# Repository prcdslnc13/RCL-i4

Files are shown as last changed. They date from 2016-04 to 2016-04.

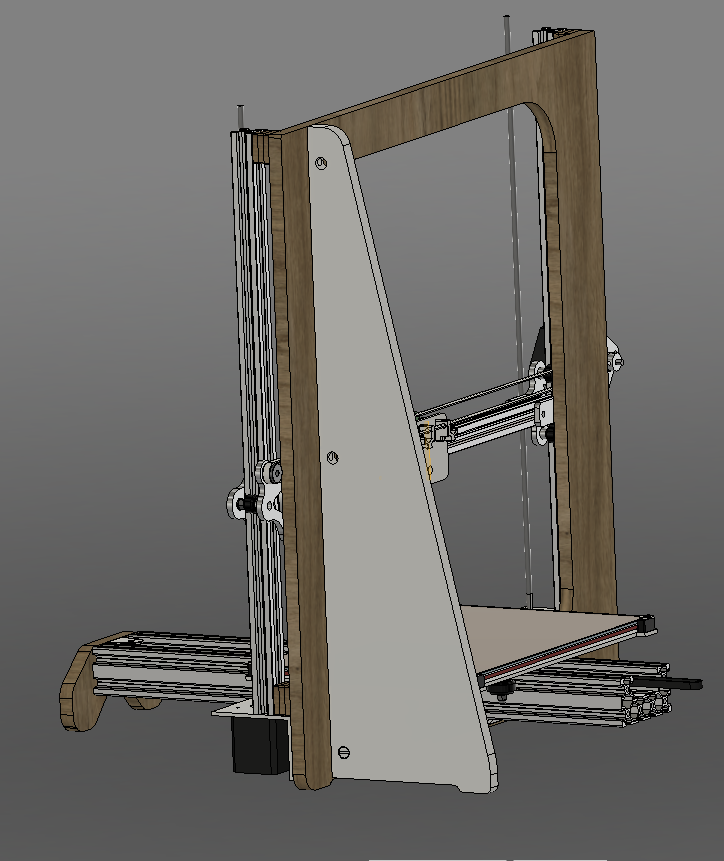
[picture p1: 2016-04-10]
pictures/2015-12-29 17_39_27-Autodesk Fusion 360.png

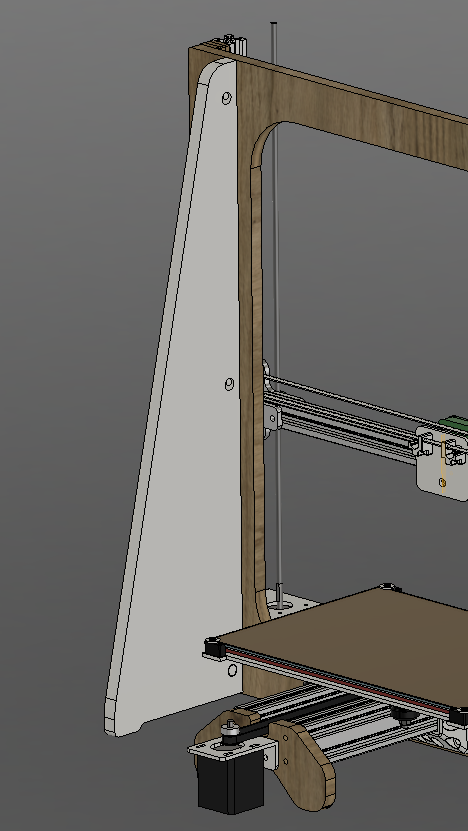
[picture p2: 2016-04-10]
pictures/2015-12-29 17_40_33-Autodesk Fusion 360.png

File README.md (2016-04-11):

# RCL-i4
V-Slot based 3D printer based on the general shape of a Prusa i3 but, ya know, not :D

> I know that there are currently errors with bolt length and qty in the BOM we found them in the initial build session but they have yet to be corrected.

This printer utilizes a bed leveling strategy similar to the Lulzbot Taz 6, but currently does not have the nozzle wipe or z limit activated in the start g-code or firmware,
  **Use at your own Risk**

The goal of the RCL-i4 was to create a 3D printer that would be able to quickly be created in the [RiverCityLabs.org](http://rivercitylabs.org) (RCL) maker space in Peoria, IL using their tools. The printed parts are kept to a minimum to allow for quick easy manufacture with sheet materials on either the laser cutter or the CNC router.

The entire design was created in Autodesk Fusion360 and I will be uploading the source models soon. *Sooner if there is a demand for them.*

Thanks to the following companies and individuals for giving their support, advice time to help RCL make this project possible
- [SMW3D.com](http://smw3d.com) - supplied a quick easy BOM ordering method for us
- [E3D-online.com](http://e3d-online.com) - Worked with us to figure out an easy way to do nozzle based bed leveling
- [Lulzbot.com](http://lulzbot.com) - Worked with me to give me a better under standing of how the bed leveling on the TAZ 6 was done
- https://openhardwarecoza.wordpress.com/
- Eric Lien
- [RiverCityLabs.org](http://rivercitylabs.org)

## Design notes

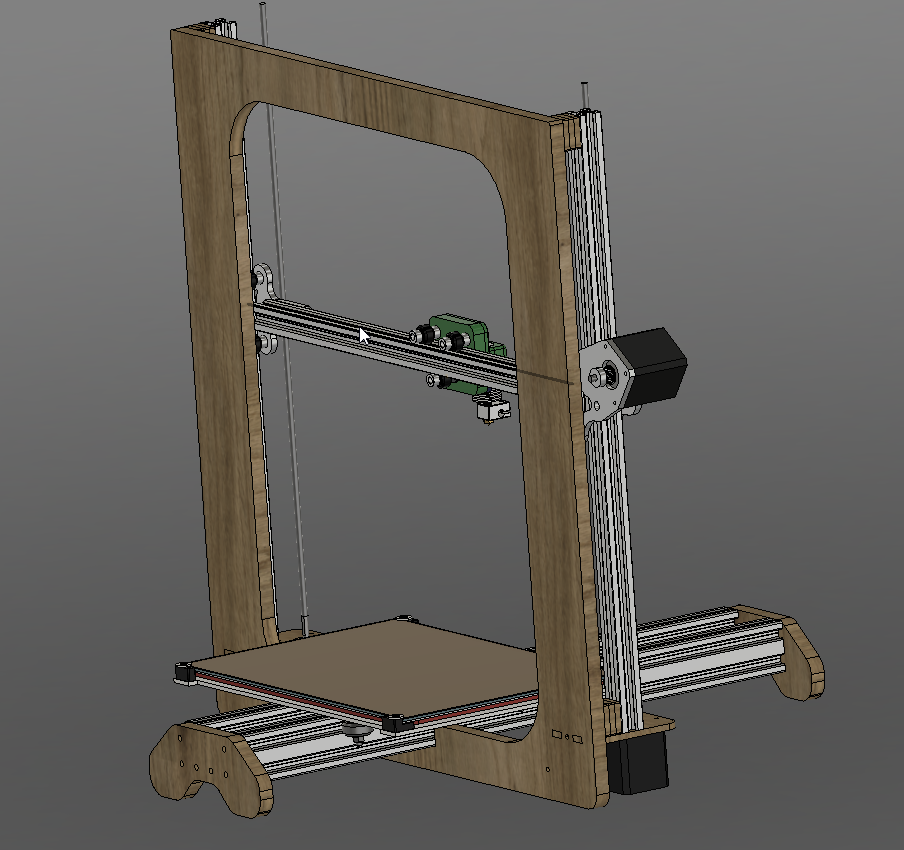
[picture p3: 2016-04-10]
pictures/2015-12-03 10_22_14-Autodesk Fusion 360.png

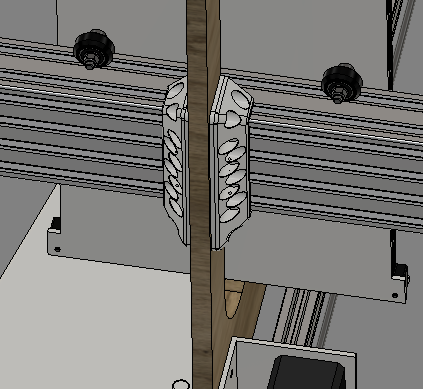
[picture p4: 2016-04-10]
pictures/2015-12-29 17_40_56-Autodesk Fusion 360.png

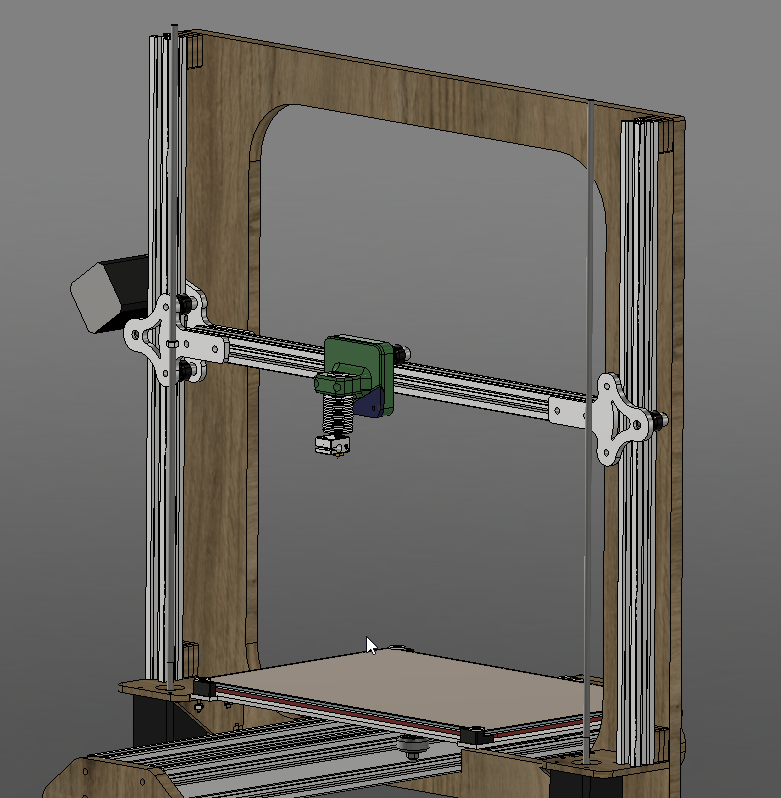
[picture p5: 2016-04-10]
pictures/2015-12-03 10_22_45-Autodesk Fusion 360.png

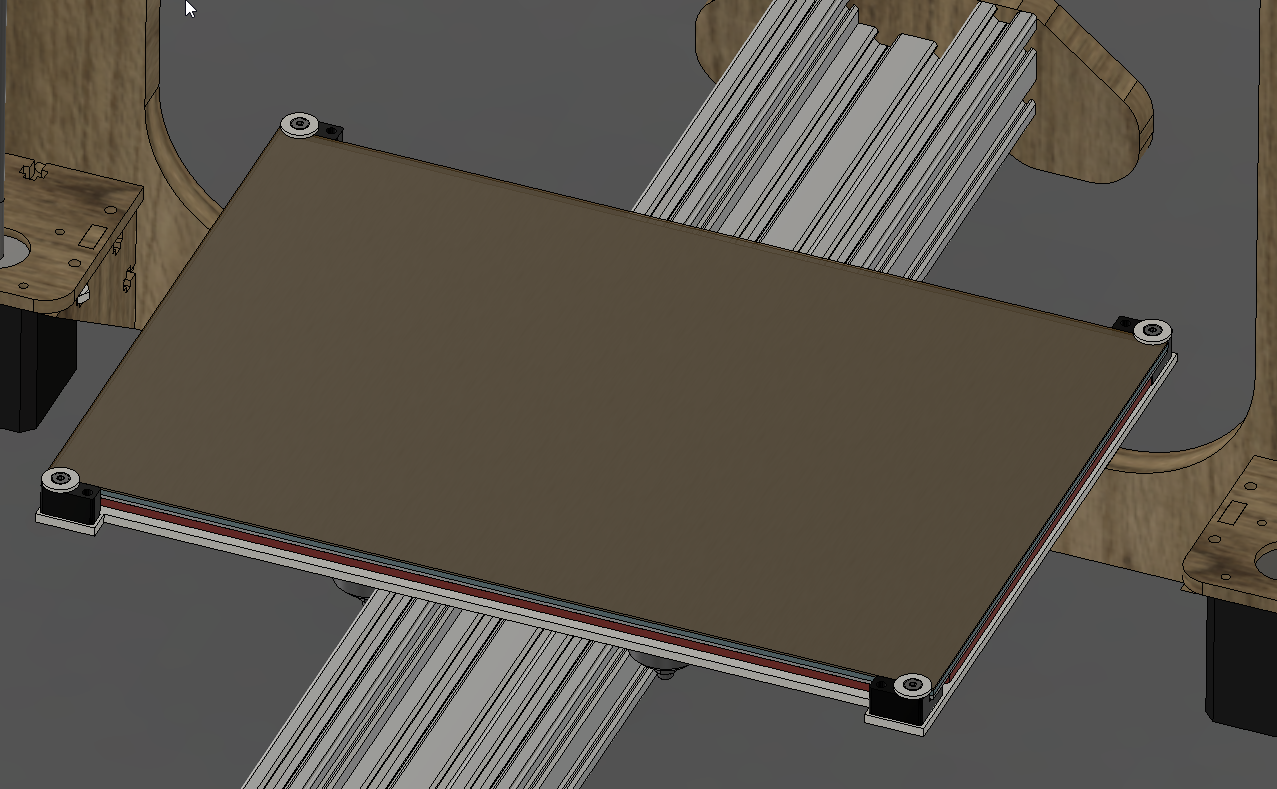
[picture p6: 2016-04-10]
pictures/2015-12-03 10_23_27-Autodesk Fusion 360.png

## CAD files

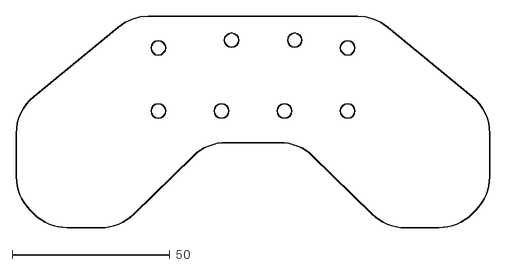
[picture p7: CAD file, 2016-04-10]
Final Dxfs/bases/front base.dxf
150.0 x 67.0

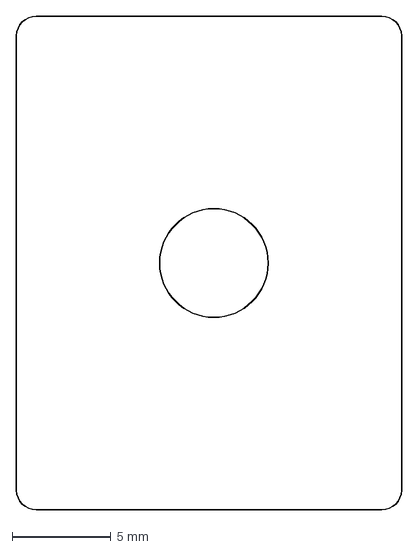
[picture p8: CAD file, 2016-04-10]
Final Dxfs/brackets/z spacer 16x.dxf
19.5 x 25.0 mm

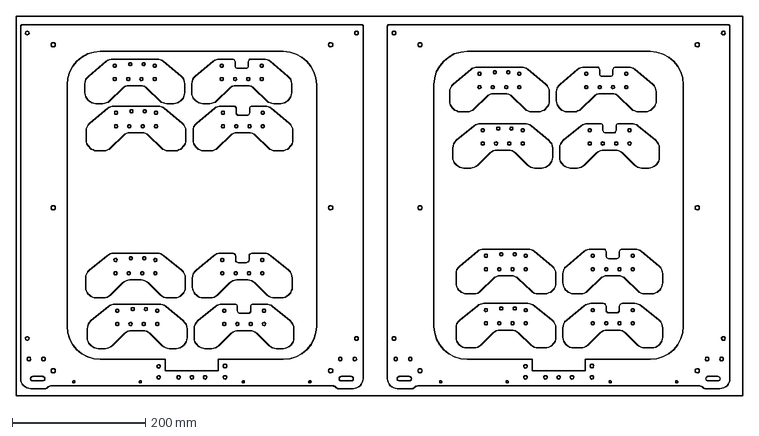
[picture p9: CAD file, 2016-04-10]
Final Dxfs/Frame/Frame cut progs/frame-cutsheet.dxf
1092.0 x 570.0 mm

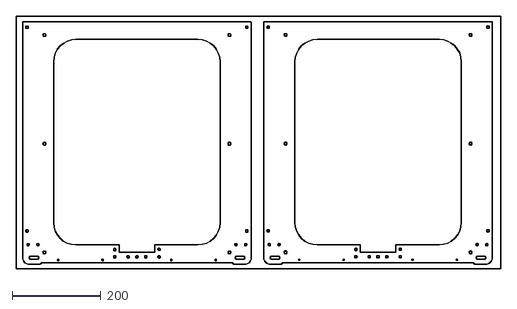
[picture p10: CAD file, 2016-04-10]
Final Dxfs/Frame/Nebula programs/frame-cutsheet nebula.dxf
1092.0 x 570.0

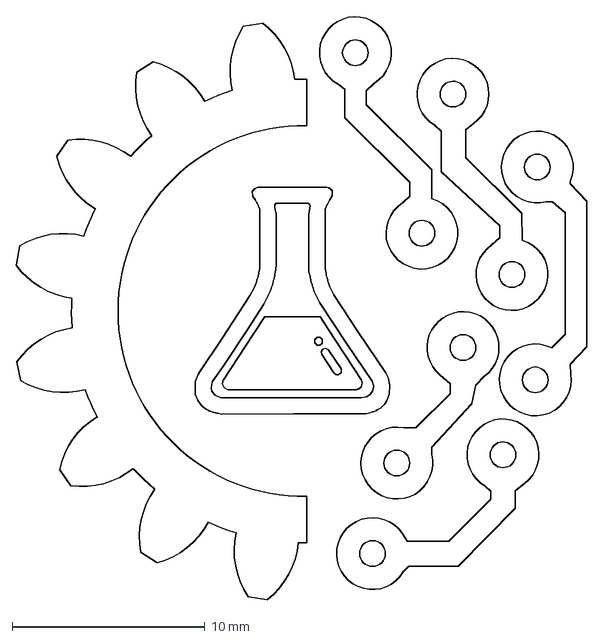
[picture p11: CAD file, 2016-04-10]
Final Dxfs/logo-for laser etch.dxf
29.6 x 30.3 mm

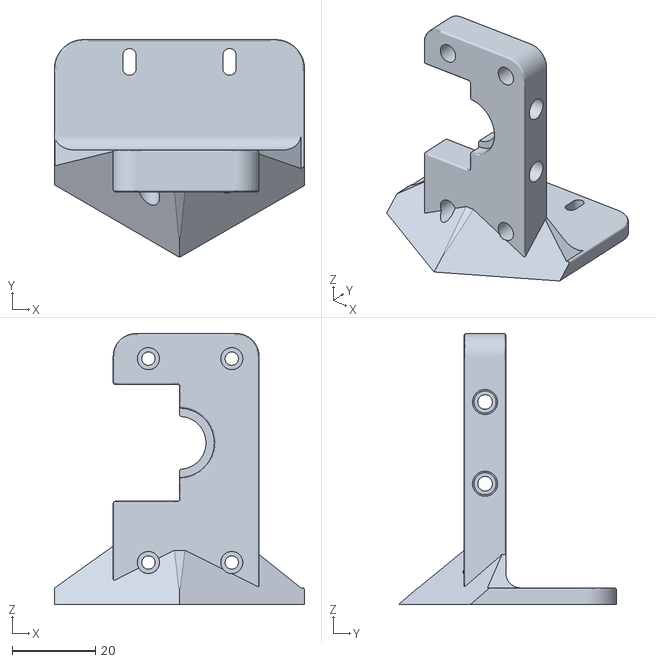
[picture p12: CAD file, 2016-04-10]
Printed Parts/bondtech mini/bondtech mount1(2).stl
60.0 x 52.2 x 65.0

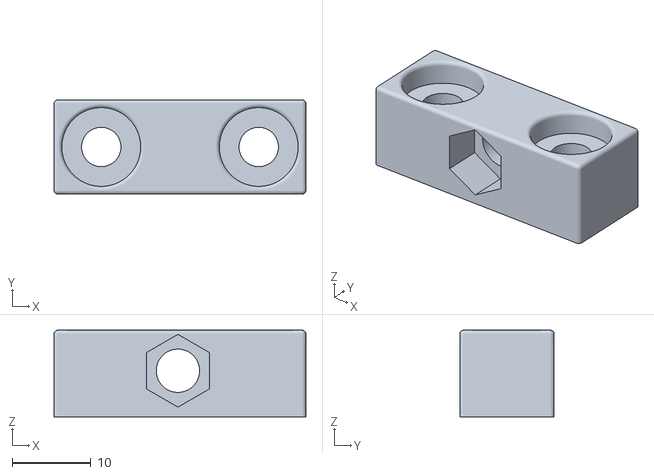
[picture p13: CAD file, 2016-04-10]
Printed Parts/Final parts/m5-nutmount.stl
32.0 x 12.0 x 11.0

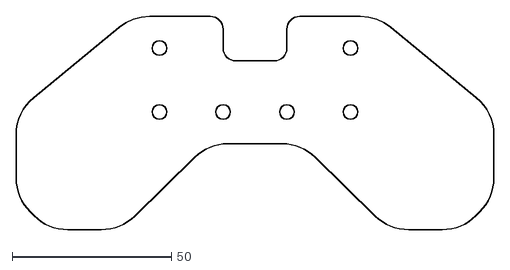
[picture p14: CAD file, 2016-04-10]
Final Dxfs/bases/rear base.dxf
150.0 x 67.0

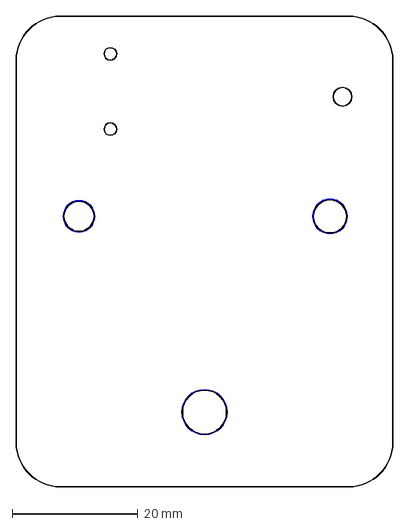
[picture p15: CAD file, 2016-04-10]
Final Dxfs/brackets/rear X-plate 3.dxf
60.0 x 75.0 mm

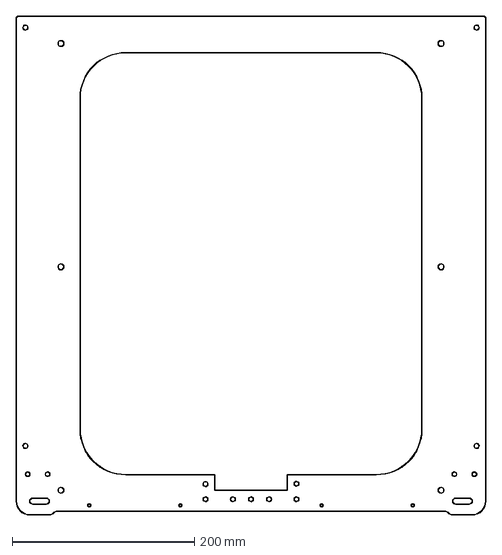
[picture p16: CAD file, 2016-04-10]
Final Dxfs/Frame/Frame cut progs/Frame.dxf
515.0 x 547.0 mm

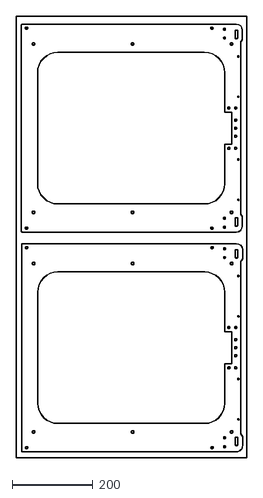
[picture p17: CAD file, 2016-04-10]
Final Dxfs/Frame/Nebula programs/frame-cutsheet nebula1.dxf
570.0 x 1092.0

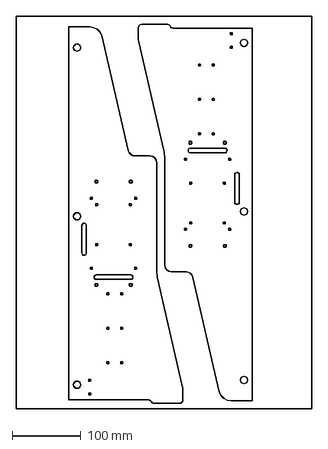
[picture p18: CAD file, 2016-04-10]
Final Dxfs/Rear Supports/rear-fin.dxf
430.0 x 570.0 mm

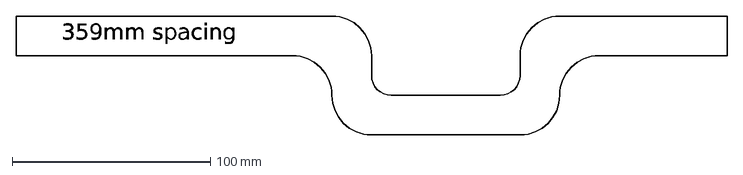
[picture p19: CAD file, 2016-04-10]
Final Dxfs/Xaxis-Spacer_jig.dxf
359mm spacing

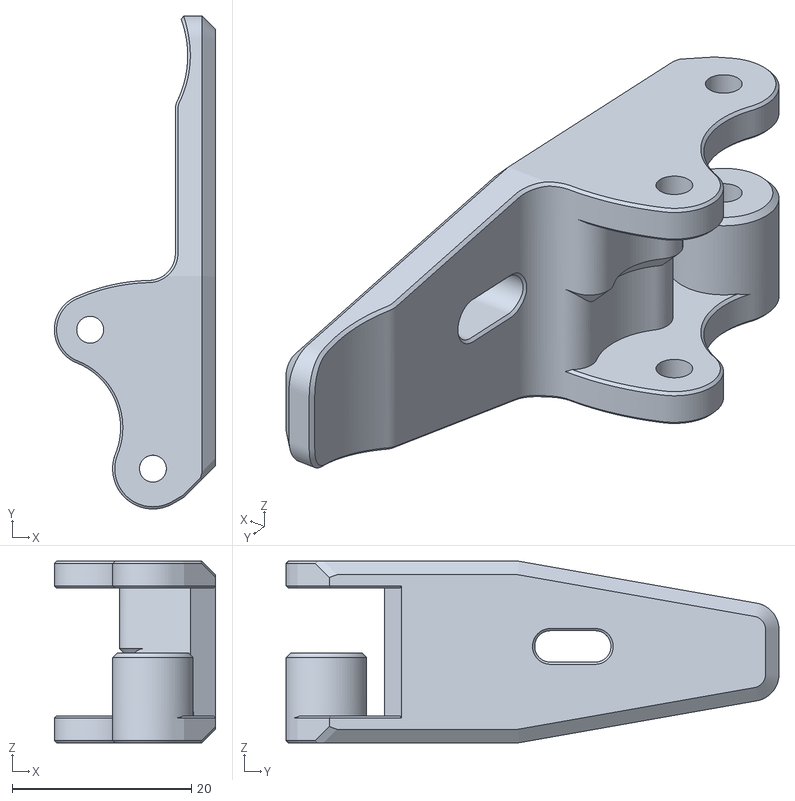
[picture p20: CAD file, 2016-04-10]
Printed Parts/bondtech mini/hindge.stl
18.0 x 55.0 x 20.2

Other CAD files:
Final Dxfs/limit holders/limit holders.dxf
Printed Parts/Final parts/Xbelt tensioner.stl
Final Dxfs/brackets/x spacer.dwg
Final Dxfs/spacing jig.dxf
Deprecated/Dep 2/Bed and brackets.dxf
Deprecated/Dep 2/MotorSide Front.dwg
Deprecated/Dep 2/MotorSide Front.dxf
Deprecated/Dep 2/MotorSide Front1.dxf
Deprecated/Dep 2/bed-cutout.dxf
Deprecated/Dep 2/front idlerside.dxf
Deprecated/Dep 2/limit holders.dwg
Deprecated/Dep 2/limit holders.dxf
Deprecated/x spacer.dxf
FIRMWARE/Marlin-RCL-i4/Marlin-RCL-i4/Documentation/Logo/Marlin Logo_old.dxf
Final Dxfs/Frame/Frame cut progs/frame-cutsheet.dwg
Final Dxfs/Rear Supports/rear-fin (1).dxf
Final Dxfs/brackets/MotorSideRear.dxf
Final Dxfs/logo-for laser etch.dwg
Printed Parts/Final parts/NozzleWiper-zmin.stl
Printed Parts/Final parts/QR MOunt.stl
Printed Parts/Final parts/bedcorner1.stl
Printed Parts/Final parts/bedcorner2.stl
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

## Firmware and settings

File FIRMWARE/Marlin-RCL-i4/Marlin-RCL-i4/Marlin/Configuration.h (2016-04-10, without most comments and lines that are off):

#define CONFIGURATION_H
#include "boards.h"
#include "macros.h"
#if ENABLED(USE_AUTOMATIC_VERSIONING)
  #include "_Version.h"
#else
  #include "Default_Version.h"
#endif
#define STRING_CONFIG_H_AUTHOR "(none, default config)" // Who made the changes.
#define SHOW_BOOTSCREEN
#define STRING_SPLASH_LINE1 SHORT_BUILD_VERSION // will be shown during bootup in line 1
#define SERIAL_PORT 0
#define BAUDRATE 115200
  #define MOTHERBOARD BOARD_AZTEEG_X3
#define EXTRUDERS 1
#define POWER_SUPPLY 1
#define TEMP_SENSOR_0 5
#define TEMP_SENSOR_1 0
#define TEMP_SENSOR_2 0
#define TEMP_SENSOR_3 0
#define TEMP_SENSOR_BED 5
#define MAX_REDUNDANT_TEMP_SENSOR_DIFF 10
#define TEMP_RESIDENCY_TIME 10  // (seconds)
#define TEMP_HYSTERESIS 3       // (degC) range of +/- temperatures considered "close" to the target one
#define TEMP_WINDOW     1       // (degC) Window around target to start the residency timer x degC early.
#define HEATER_0_MINTEMP 5
#define HEATER_1_MINTEMP 5
#define HEATER_2_MINTEMP 5
#define HEATER_3_MINTEMP 5
#define BED_MINTEMP 5
#define HEATER_0_MAXTEMP 300
#define HEATER_1_MAXTEMP 300
#define HEATER_2_MAXTEMP 275
#define HEATER_3_MAXTEMP 275
#define BED_MAXTEMP 150
#define PIDTEMP
#define BANG_MAX 255 // limits current to nozzle while in bang-bang mode; 255=full current
#define PID_MAX BANG_MAX // limits current to nozzle while PID is active (see PID_FUNCTIONAL_RANGE below); 255=full current
  #define PID_FUNCTIONAL_RANGE 10 // If the temperature difference between the target temperature and the actual temperature
  #define PID_INTEGRAL_DRIVE_MAX PID_MAX  //limit for the integral term
  #define K1 0.95 //smoothing factor within the PID
      #define DEFAULT_Kp 25.67
      #define DEFAULT_Ki 4.75
      #define DEFAULT_Kd 34.69
#define MAX_BED_POWER 255 // limits duty cycle to bed; 255=full current
#define PREVENT_DANGEROUS_EXTRUDE
#define PREVENT_LENGTHY_EXTRUDE
#define EXTRUDE_MINTEMP 170
#define EXTRUDE_MAXLENGTH (X_MAX_LENGTH+Y_MAX_LENGTH) //prevent extrusion of very large distances.
#define THERMAL_PROTECTION_HOTENDS // Enable thermal protection for all extruders
#define THERMAL_PROTECTION_BED     // Enable thermal protection for the heated bed
#define ENDSTOPPULLUPS // Comment this out (using // at the start of the line) to disable the endstop pullup resistors
const bool X_MIN_ENDSTOP_INVERTING = true; // set to true to invert the logic of the endstop.
const bool Y_MIN_ENDSTOP_INVERTING = true; // set to true to invert the logic of the endstop.
const bool Z_MIN_ENDSTOP_INVERTING = true; // set to true to invert the logic of the endstop.
const bool X_MAX_ENDSTOP_INVERTING = true; // set to true to invert the logic of the endstop.
const bool Y_MAX_ENDSTOP_INVERTING = true; // set to true to invert the logic of the endstop.
const bool Z_MAX_ENDSTOP_INVERTING = false; // set to true to invert the logic of the endstop.
const bool Z_MIN_PROBE_ENDSTOP_INVERTING = true; // set to true to invert the logic of the endstop.
#define X_ENABLE_ON 0
#define Y_ENABLE_ON 0
#define Z_ENABLE_ON 0
#define E_ENABLE_ON 0 // For all extruders
#define DISABLE_X false
#define DISABLE_Y false
#define DISABLE_Z false
#define DISABLE_E false // For all extruders
#define DISABLE_INACTIVE_EXTRUDER true //disable only inactive extruders and keep active extruder enabled
#define INVERT_X_DIR false
#define INVERT_Y_DIR true
#define INVERT_Z_DIR false
#define INVERT_E0_DIR false
#define INVERT_E1_DIR false
#define INVERT_E2_DIR false
#define INVERT_E3_DIR false
#define X_HOME_DIR -1
#define Y_HOME_DIR -1
#define Z_HOME_DIR -1
#define min_software_endstops true // If true, axis won't move to coordinates less than HOME_POS.
#define max_software_endstops true  // If true, axis won't move to coordinates greater than the defined lengths below.
#define X_MIN_POS 0
#define Y_MIN_POS 0
#define Z_MIN_POS 0
#define X_MAX_POS 300
#define Y_MAX_POS 220
#define Z_MAX_POS 200
#define AUTO_BED_LEVELING_FEATURE // Delete the comment to enable (remove // at the start of the line)
#define Z_MIN_PROBE_REPEATABILITY_TEST  // If not commented out, Z-Probe Repeatability test will be included if Auto Bed Leveling is Enabled.
  #define AUTO_BED_LEVELING_GRID
    #define LEFT_PROBE_BED_POSITION 10
    #define RIGHT_PROBE_BED_POSITION 287
    #define FRONT_PROBE_BED_POSITION 0
    #define BACK_PROBE_BED_POSITION 208
    #define MIN_PROBE_EDGE 10 // The Z probe minimum square sides can be no smaller than this.
    #define AUTO_BED_LEVELING_GRID_POINTS 2
  #define X_PROBE_OFFSET_FROM_EXTRUDER 0     // Z probe to nozzle X offset: -left  +right
  #define Y_PROBE_OFFSET_FROM_EXTRUDER 0     // Z probe to nozzle Y offset: -front +behind
  #define Z_PROBE_OFFSET_FROM_EXTRUDER -1.2  // Z probe to nozzle Z offset: -below (always!) JMS
  #define Z_RAISE_BEFORE_HOMING 4       // (in mm) Raise Z axis before homing (G28) for Z probe clearance.
  #define XY_TRAVEL_SPEED 8000         // X and Y axis travel speed between probes, in mm/min.
  #define Z_RAISE_BEFORE_PROBING 15   // How much the Z axis will be raised before traveling to the first probing point.
  #define Z_RAISE_BETWEEN_PROBINGS 5  // How much the Z axis will be raised when traveling from between next probing points.
  #define Z_RAISE_AFTER_PROBING 15    // How much the Z axis will be raised after the last probing point.
  #define Z_SAFE_HOMING   // This feature is meant to avoid Z homing with Z probe outside the bed area.
    #define Z_SAFE_HOMING_X_POINT ((X_MIN_POS + X_MAX_POS) / 2)    // X point for Z homing when homing all axis (G28).
    #define Z_SAFE_HOMING_Y_POINT ((Y_MIN_POS + Y_MAX_POS) / 2)    // Y point for Z homing when homing all axis (G28).
#define HOMING_FEEDRATE {50*60, 50*60, 4*60, 0}  // set the homing speeds (mm/min)
#define DEFAULT_AXIS_STEPS_PER_UNIT   {80,80,400,141}  // {80,80,4000,141} for m5 threaded rod
#define DEFAULT_MAX_FEEDRATE          {300, 300, 2.5, 25}    // (mm/sec)
#define DEFAULT_MAX_ACCELERATION      {3000,3000,100,10000}    // X, Y, Z, E maximum start speed for accelerated moves. E default values are good for Skeinforge 40+, for older versions raise them a lot.
#define DEFAULT_ACCELERATION          3000    // X, Y, Z and E acceleration in mm/s^2 for printing moves
#define DEFAULT_RETRACT_ACCELERATION  3000    // E acceleration in mm/s^2 for retracts
#define DEFAULT_TRAVEL_ACCELERATION   3000    // X, Y, Z acceleration in mm/s^2 for travel (non printing) moves
#define DEFAULT_XYJERK                20.0    // (mm/sec)
#define DEFAULT_ZJERK                 0.4     // (mm/sec)
#define DEFAULT_EJERK                 5.0    // (mm/sec)
#define CUSTOM_M_CODES
    #define CUSTOM_M_CODE_SET_Z_PROBE_OFFSET 851
    #define Z_PROBE_OFFSET_RANGE_MIN -20
    #define Z_PROBE_OFFSET_RANGE_MAX 20
#define PLA_PREHEAT_HOTEND_TEMP 180
#define PLA_PREHEAT_HPB_TEMP 70
#define PLA_PREHEAT_FAN_SPEED 0   // Insert Value between 0 and 255
#define ABS_PREHEAT_HOTEND_TEMP 240
#define ABS_PREHEAT_HPB_TEMP 110
#define ABS_PREHEAT_FAN_SPEED 0   // Insert Value between 0 and 255
#define LANGUAGE_INCLUDE GENERATE_LANGUAGE_INCLUDE(en)
  #define DISPLAY_CHARSET_HD44780_JAPAN        // this is the most common hardware
#define SOFT_PWM_SCALE 0
#define FILAMENT_SENSOR_EXTRUDER_NUM 0   //The number of the extruder that has the filament sensor (0,1,2)
#define MEASUREMENT_DELAY_CM        14   //measurement delay in cm.  This is the distance from filament sensor to middle of barrel
#define DEFAULT_NOMINAL_FILAMENT_DIA 3.00  //Enter the diameter (in mm) of the filament generally used (3.0 mm or 1.75 mm) - this is then used in the slicer software.  Used for sensor reading validation
#define MEASURED_UPPER_LIMIT         3.30  //upper limit factor used for sensor reading validation in mm
#define MEASURED_LOWER_LIMIT         1.90  //lower limit factor for sensor reading validation in mm
#define MAX_MEASUREMENT_DELAY       20     //delay buffer size in bytes (1 byte = 1cm)- limits maximum measurement delay allowable (must be larger than MEASUREMENT_DELAY_CM  and lower number saves RAM)
#define DEFAULT_MEASURED_FILAMENT_DIA  DEFAULT_NOMINAL_FILAMENT_DIA  //set measured to nominal initially
#include "Configuration_adv.h"
#include "thermistortables.h"
